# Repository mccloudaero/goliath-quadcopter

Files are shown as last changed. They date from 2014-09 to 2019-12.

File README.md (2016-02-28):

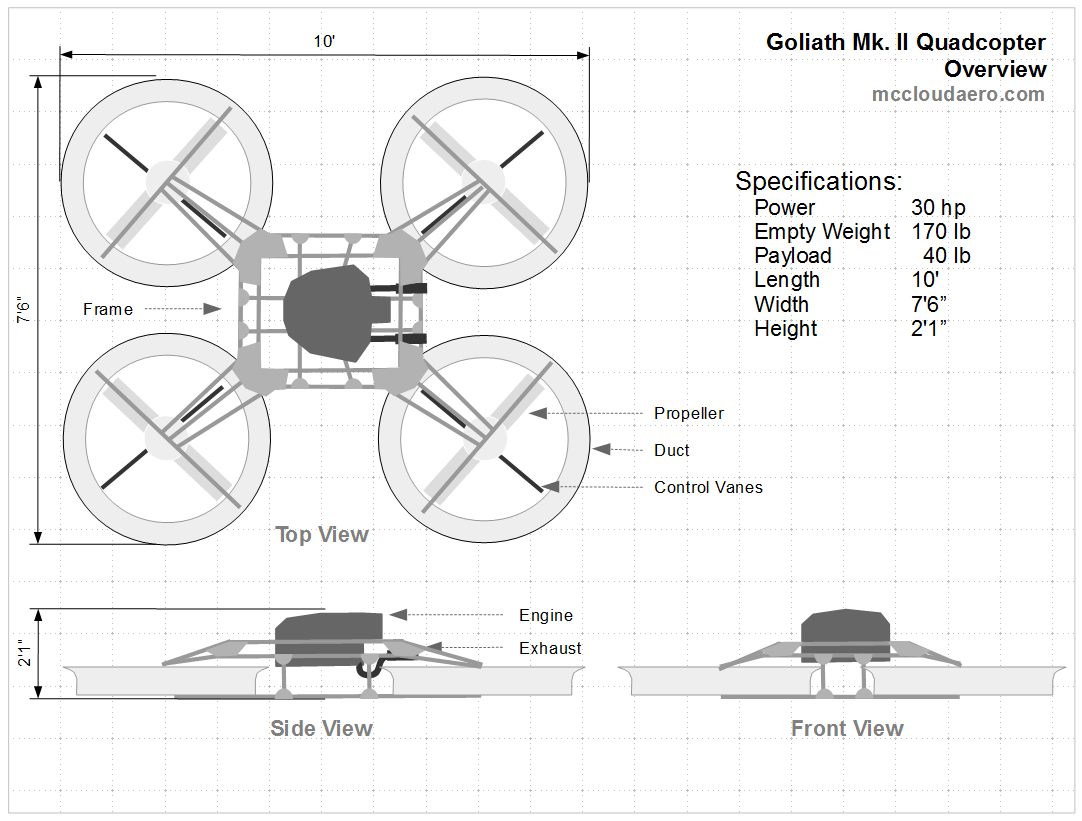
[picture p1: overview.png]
Overview

# Goliath Quadcopter
This repository contains the design data for the Goliath Quadcopter designed by
[McCloud Aero Corp](http://www.mccloudaero.com). The primary documentation source can be found at the
[Hackaday Project Page](https://hackaday.io/project/1230-goliath-a-gas-powered-quadcopter)

### Overview
Goliath is a prototype vehicle for developing large scale quadcopters. The design is based on a single central gas engine with a belt drive providing power to the four propellers. Control is done using control vanes placed under the propellers. Each propeller is enclosed within a duct that protects the rotors and contributes to the lift. Goliath itself will be open source with the creative commons license, and whenever possible open source components were used. It's currently a work in progress, and even when completed it's intended as a starting point for future vehicles.

### [Avionics](https://github.com/mccloudaero/goliath-quadcopter/blob/master/avionics/README.md)
### [Drive System](https://github.com/mccloudaero/goliath-quadcopter/blob/master/drive_system/README.md)
### Electrical System
### Structure

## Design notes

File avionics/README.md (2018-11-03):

# Avionics
### Overview
This file is intended as a guide for setting up the avionics for Goliath. Goliath uses the [Pixhawk2](https://docs.px4.io/en/flight_controller/pixhawk-2.html) flight controller running the [PX4](https://px4.io) flight stack.

## Basic Setup
### Install QGroundControl on your computer
QGroundControl is a software an open source micro air vehicle ground control station [QGroundControl](http://qgroundcontrol.com). In addition to being able to provide mission control for Goliath, it also provides an easy way to load the latest version of the Firmware.

### Controller Setup
The Taranis X9D is the controller recommended for the Pixhawk. General information on setting up the Taranis with the Pixhawk can be found on the Pixhawk user guide at:
[Pixhawk Flight Mode Configuration](http://px4.io/docs/flight-mode-configuration/)
Follow the instructions for setting up the controller for Single Channel Flight Mode Configuration in the video.
[Controller Setup](http://https://youtu.be/scqO7vbH2jo)

####Flight Modes
Switches SE and SF are used together to cycle through the different modes.

Num | Mode | Switch
---|---|---
1|Stabalized/Main|SF back, SE back
2|Acro|SF back, SE mid
3|Altitude Control|SF back, SE front
4|Position Control|SF front, SE front
5|Loiter|SF front, SE mid
6|Return|SF front, SE back

####Goliath specific configuration
Additional channels are required for Goliath to control the gas engine. Setup the controller with the following channels: 

Channel | Source | Function
---|---|---
CH6 | S2 | choke servo
CH7 | SH | starter relay
CH8 | SD | ignition relay

### Firmware Update
Goliath requires special drivers for PX4, and therefore a custom Firmware update. Following the instructions found in /goliath_px4_firmware_patch/README.md

### Customize Configuration
While, the Pixhawk firmware does not require modification, the controller does need custom configuration for Goliath.

Copy /etc in the avionics directory to the SD card.

* /etc/config.txt 
  Sets up the custom configuration for Goliath, specifies which mixers to use 

* /etc/extras.txt 
  Starts the driver for the EVPR master node 

* /etc/mixers
  Custom mixers for goliath

Details on how to make custom mixer files can be found at http://dev.px4.io/concept-mixing.html

#### AUX Servos
The configuration of the Aux output pins is controlled by the fmu app (https://pixhawk.org/firmware/apps/fmu). The mode needed for Goliath's configuration is:
mode_pwm_gpio
This mode enables SRV1-SRV4 and GPIO_EXT1 and GPIO_EXT2

System start-up commands can be changed using the following guide.
http://dev.px4.io/advanced-system-startup.html

More informatition on customization of the PX4 flight stack can be found at:<br>
[Pixhawk: System Startup](http://dev.px4.io/advanced-system-startup.html)<br>
[Pixhawk: Adding A New Airframe](http://dev.px4.io/airframes-adding-a-new-frame.html)

#### Debugging 
Dev Guide on how to connect to the system console:
http://dev.px4.io/advanced-system-console.html

### Theory of Operation
After ensuring that the area is clear, the first step is to set the master switch to ON. At this point the flight controller will power up and start in safe mode (Main LED will be breathing). While in safe mode, all of the servos and relays are disabled from being activated by the firmware. Once it's confirmed that the firmware is operating nominally, the operator can take the system out of safe mode. At this point all of the controls can be checked out prior to starting the engine. If all of the controls are working nominally, the engine can then be started. The engine ignition relay is enabled, allowing the engine to run. Next, the starter is used to start the engine.

### Arming and Disarming
#### From the Control Stick
##### Arming
1. Ensure the Main LED is breathing.
2. Press and hold the safety switch for 3 seconds. The light on the safety switch will start blinking differently.
3. Place the throttle stick in the bottom right corner and hold for 5 seconds. The main LED will become solid.
##### Disarming
To disarm, place the throttle stick in the bottom left corner.

#### Ground Station
Alternatively arming and disarming can also be performed in QGroundControl.

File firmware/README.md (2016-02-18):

# Firmware
### Overview
This file is intended as a guide for setting up the firmware for Goliath. Goliath uses the [Pixhawk](http://www.pixhawk.org) flight controller. The Pixhawk hardware is open source and is capable of running different flight stacks. For Goliath, the PX4 flight stack was chosen.

### Firmware Setup
Before getting started with the firmware, the tool chains need to be setup for compiling the firmware. While the firmware can be compiled on most operating systems, it's really recommended to use Linux, particularly Ubuntu, as it has the most support. The instructions for setting up the tools chains for Linux can be found at:
[Linux Tool Chain Setup](http://dev.px4.io/starting-installing-linux.html)

Once the tool chain has been setup, simply follow the instructions for downloading and compiler the firmware:
[Building the Firmware](http://dev.px4.io/starting-building.html)

### Firmware Configuration
The PX4 flight stack is able to be used for different airframes though the use of mixers. The mixer tells the flight stack how to take the input values and translate them to the output values, so that the control software can be universally applied and eliminates the need for custom firmware. The guide for added custom airframes is at:
[Adding a new Airframe Configuration](http://dev.px4.io/airframes-adding-a-new-frame.html)
[Old Guide - Deprecated](https://pixhawk.org/dev/mixing)

The custom mixer file for Goliath will be located in this folder.

### Theory of Operation
After ensuring that the area is clear, the first step is to set the master switch to ON. At this point the Pixhawk controller will power up and start in safe mode. While in safe mode, all of the servos and relays are disabled from being activated by the firmware. Once it's confirmed that the firmware is operating nominally, the operator can take the system out of safe mode. At this point all of the controls can be checked out prior to starting the engine. If all of the controls are working nominally, the engine can then be started. The engine ignition relay is enabled, allowing the engine to run. Next, the starter is used to start the engine.

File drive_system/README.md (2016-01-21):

# Drive System
### Overview
Goliath uses a single 30 Hp engine and a belt system to transfer power to the four propellers. A single motor was chosen over four smaller engines because of the larger power to weight ratio than a single larger engine. High Torque Drive (HTD) belts were selected because they are able to transfer more power per weight than roller chain and can also run at higher RPMs that Goliath requires.

### Belts vs. Roller Chains
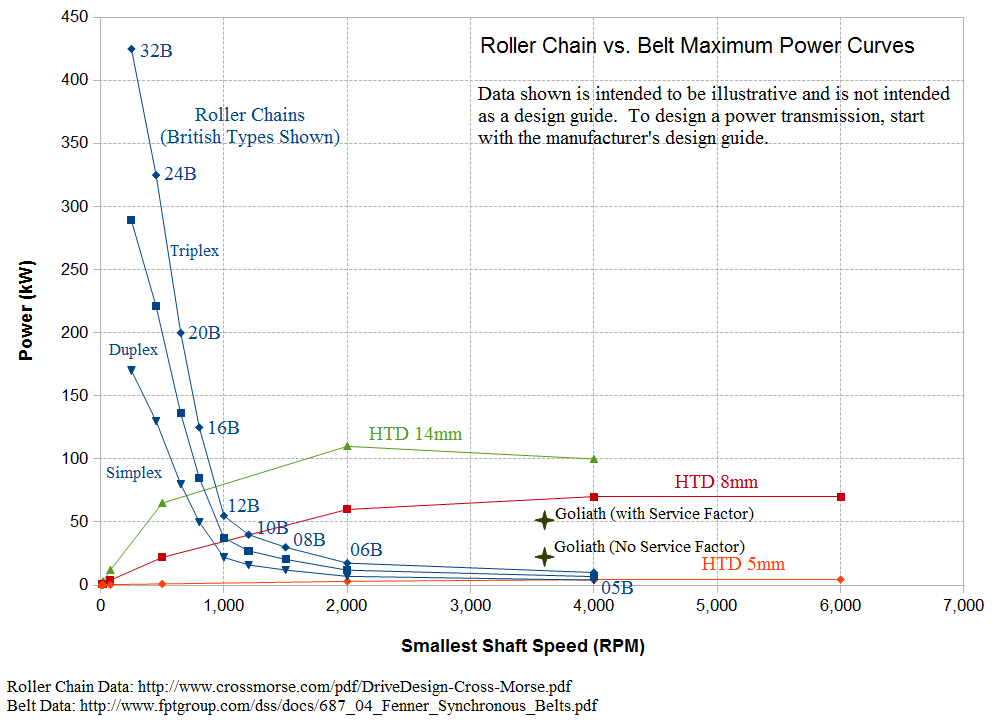
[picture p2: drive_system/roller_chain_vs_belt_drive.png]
Belt vs Rollers


### Belt and Pulley Layout
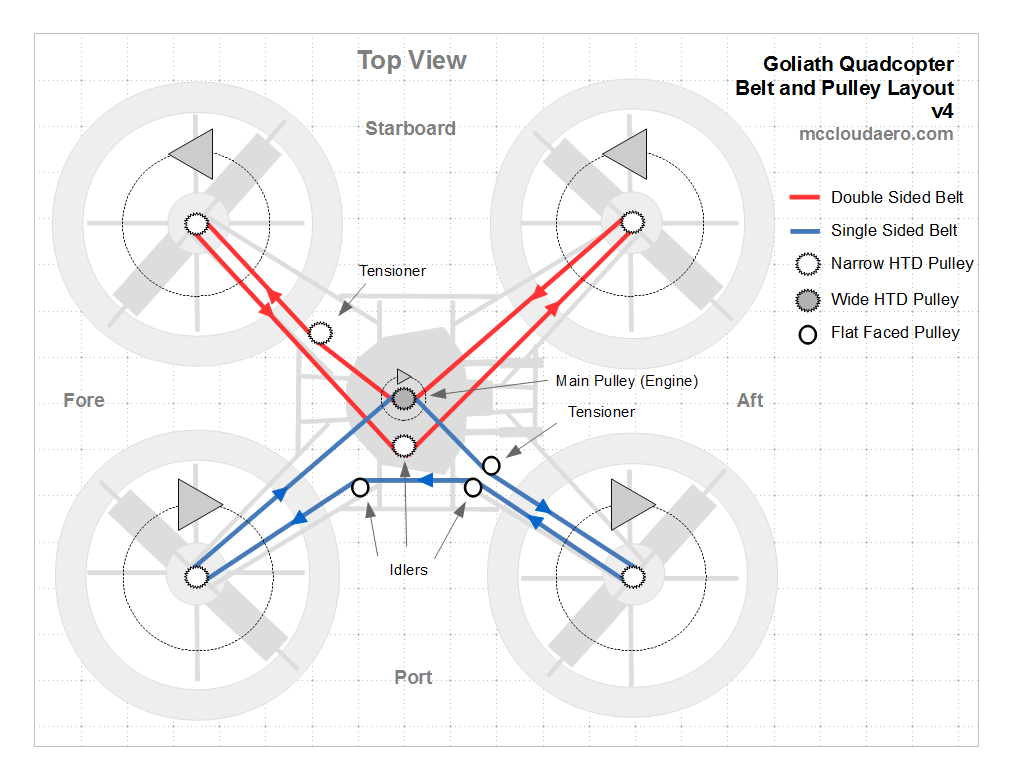
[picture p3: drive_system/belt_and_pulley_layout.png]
Drive System


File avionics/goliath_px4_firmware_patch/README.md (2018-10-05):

# PX4 Firmware patch
Adds drivers for:
* EVPR Master Node
* GPIO Relays

# Firmware Setup
## Checkout Firmware from
https://github.com/PX4/Firmware.git

## Apply Patch
git apply <path to patch>

## Compile
make px4fmu-v3_default

## Flash
make px4fmu-v3_default upload

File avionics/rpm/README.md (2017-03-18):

# RPM Sensor

## Frequency Measurement
The frequency is measured using a hall effect sensor connected to a [Trinket Pro](https://www.adafruit.com/product/2000).

# Trinket Pro
Pin | Purpose
---|---
BAT+|Power to Trinket Pro
GND|Ground
3|Hall Effect Signal
5V(Header)|Hall Effect Power
GND(Header)|Hall Effect Ground 
A4|SDA for I2C
A5|SCL for I2C

## Pixhawk I2C Port pinout
Pin | Signal | Volt
---|---|---
1(red)|VCC|+5
2(blk)|SCL|+3.3(pullups)
3(blk)|SDA|+3.3(pullups)
4(blk)|GND|GND

## References
[Additional Trinket Pro Info] (https://learn.adafruit.com/introducing-pro-trinket/downloads)
[Trinket Pro Pinout] (https://learn.adafruit.com/introducing-pro-trinket/pinouts)

[Adafruit IDE Setup] (https://learn.adafruit.com/adafruit-arduino-ide-setup/overview)

[Hall Effect Sensor Example] (https://diyhacking.com/arduino-hall-effect-sensor-tutorial/)

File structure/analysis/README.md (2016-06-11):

#Analysis Overview
Analysis done with Frame3DD
[Frame3DD](http://frame3dd.sourceforge.net/).

##Linux Install (Ubuntu 14.04)
1. Download Frame3DD source
2. Go to Frame3DD/src and run make
3. mv frame3dd ../
4. ensure gnuplot is installed
5. run

##Run Analysis Case
frame3dd frame.3dd frame.out

##Post-Processing
After the analysis is complete, and the frame design is satisfactory, the results are post-processed. This is done to obtain the total lengths of the tubing required and to get the frame nodes coordinates to build a CAD object.

./framepost.py

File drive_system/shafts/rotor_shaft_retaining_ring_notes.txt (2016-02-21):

Retaining Rings for 3/4" shaft (McMaster-Carr 96363A578)
Groove Width Required: 0.047" (+0.003" -0.000")
Groove Depth Required: 0.023"

Load Capacity 1,218 lbs

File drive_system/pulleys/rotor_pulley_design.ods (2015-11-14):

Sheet: Dimensions
Pulley Type | HTD
Teeth | 40
Tooth Type | 8M
Belt Width | 30 | mm
Pulley Width | 31.877 | mm
Flange Width | 2 | mm
Total Width Required | 35.877 | mm
Idler | SH-BB
Width | 33.3375
Width Difference | 2.5395 | mm | (Positive OK, Negative, need more material)
Bearing
Model | 7868-5tn
Make | Nice
Bore | 5/8”
OD | 40 | mm
Width | 18.25625 | mm | 0.71875 | in
Propeller Thickness | 46.0375 | mm | 1.8125 | in
Bolt Length
Stackup | 81.9145 | mm | 3.224980315 | in
(Pulley+Propeller)
Bolt Length |  |  | 3.75 | in

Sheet: Machining Operations
Machining Operations | Tool
Part Off Pulley | Parting Tool
Center Bore | Drill

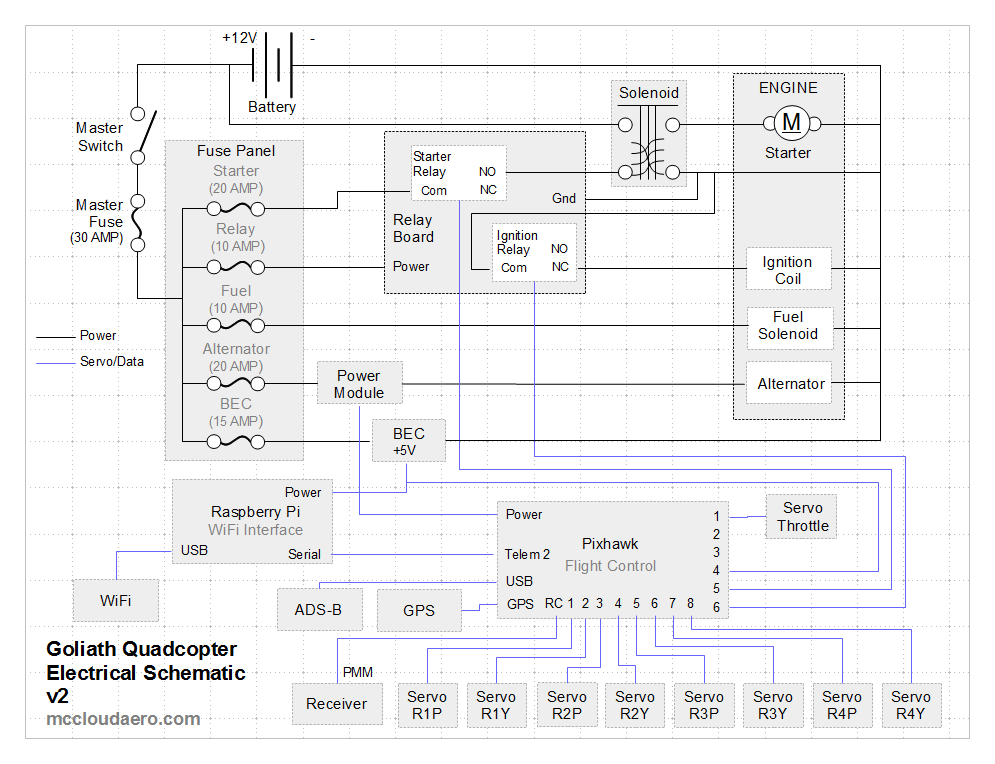
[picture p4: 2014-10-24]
electrical_system/electrical_schematic.png

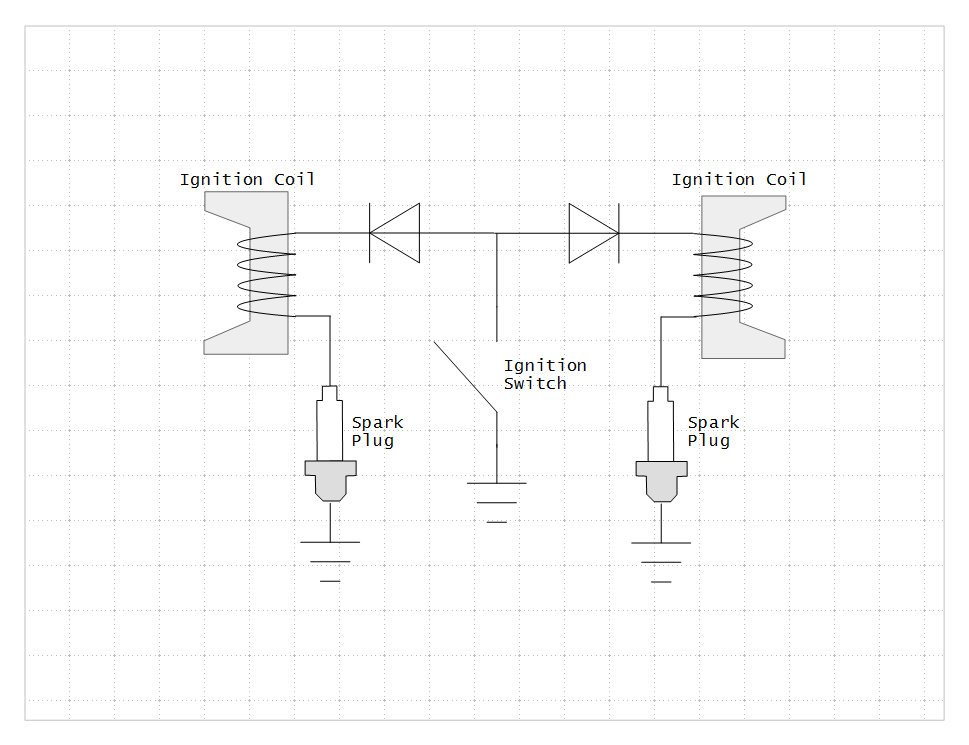
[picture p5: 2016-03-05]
electrical_system/ignition_schematic.png

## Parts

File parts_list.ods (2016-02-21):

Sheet: Parts
Part | Category | Qty | Description | Part No | Supplier | Weight | Sub Total Weight | Price | Sub Total | Link | CAD? | Source | Sub Total | Addtional Info
Engine | Engine | 1 | 1-1/8-Inch by 7/16-20-Inch Shaft Briggs and Stratton Professional Series 30 Gross HP 810 cc V-Twin 1-1/8-Inch by 7/16-20-Inch Shaft | 49M977-1036-G5 | Equipatron | 84.00 | 84.00 | $899.00 | $899.00 | http://www.equipatron.com/briggs-stratton-vertical-engine-49m977-1036-g5.html | No | web | 84 | http://www.briggsandstratton.com/us/en/engines/rider-mower-engines/professional-series-efm
Upper Drive Belt | Drive System | 1 | Double Sided HTD Belt 30mm wide 4960mm Long |  |  | 1.10 | 1.10 |  |  | http://www.bbman.com/catalog/product/4960-8M-20 |  | web | 1.1
Lower Drive Belt | Drive System | 1 | Double Sided HTD Belt 30mm wide 4400mm Long |  |  | 1.10 | 1.10 |  |  | http://www.bbman.com/catalog/product/4400-8M-20 |  | web | 1.1
Engine Bushing | Drive System | 1 | Quick-Disconnect (QD) Bushing Style SH, 1-1/8" Bore, 1/4" x 1/8" Keyway | SHX1-1/8 | B&B Manufacturing | 1.00 | 1.00 | $9.50 | $9.50 | http://www.bbman.com/catalog/product/SHX1-1_8 | Yes | web | 1
Engine Pulley | Drive System | 1 | Pulley 8mm Pitch, 50mm Wide Belt, QD Bushing, Style SH, 3.819" OD, 34 Teeth | QD34-8M-50 | B&B Manufacturing | 2.60 | 2.60 | $84.00 | $84.00 | http://www.bbman.com/catalog/product/QD34-8M-50 | Yes | web | 5.2
Rotor Pulley | Drive System | 4 | Pulley 8mm Pitch, 30mm Wide 44 Teeth |  | McCloud Aero | 1.75 | 7.00 | $101.59 | $406.36 |  | Yes | web | 5.52
Rotor (CW) |  | 2 |  |  | McCloud Aero | 1.25 | 2.50 | $30.00 | $60.00 |  | Yes | est | 20
Rotor (CCW) |  | 2 |  |  | McCloud Aero | 1.25 | 2.50 | $30.00 | $60.00 |  | Yes | est | 20
Rotor Bolt | Drive System | 24 | 1/4”-20 bolts 3 3/4” long, grade 8 | 91257A557 | McMaster-Carr |  | 0.00 | $0.51 | $12.87
Rotor Shaft | Drive System | 4 | 5/8” diameter, 12” long shaft | 5947k14 | McMaster-Carr | 1.25 | 5.00 | 12.13 | $48.52 | http://www.mcmaster.com/#5947k14/=zzzib2
Center Beam – A | Structure | 1 | Slotted Angle 2 1/2” x 1 1/2” x 39 3/4” |  |  | 2.78 | 2.78
Center Beam – B | Structure | 1 | Slotted Angle 2 1/2” x 1 1/2” x 39 3/4” |  |  | 2.78 | 2.78
Center Beam – C | Structure | 1 | Slotted Angle 1 1/2” x 1 1/2” x 39 3/4” |  |  |  | 0.00
Center Beam – D | Structure | 1 | Slotted Angle 1 1/2” x 1 1/2” x 39 3/4” |  |  |  | 0.00
End Beam | Structure | 4 | Slotted Angle 2 1/2” x 1 1/2” x 18” |  |  | 1.26 | 5.04
Cross Beam | Structure | 4 | Slotted Angle 2 1/2” x 1 1/2” x 30” |  |  | 2.10 | 8.40
Side Beam – A | Structure | 2 | Slotted Angle 2 1/2” x 1 1/2” x 29 1/4” |  |  | 2.05 | 4.10
Side Beam – B | Structure | 2 | Slotted Angle 2 1/2” x 1 1/2” x 29 1/4” |  |  | 2.05 | 4.10
Prop Mount | Structure | 8 | Slotted Angle 2 1/2” x 1 1/2” x 6” |  |  | 0.42 | 3.36
Outer Prop Support | Structure | 8
Inner Prop Support – A | Structure | 4
Inner Prop Support – B | Structure | 4
Side Cross Bar | Structure | 4 | Slotted Flat 1 1/2” x 30” |  |  |  | 0.00
End Cross Bar | Structure | 4 | Slotted Flat 1 1/2” x 18” |  |  |  | 0.00
Engine Bolts | Structure | 4
 |  |  |  |  |  |  | 137.355

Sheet: Raw Materials
Material | Qty | Part No. | Supplier | Price | Sub-Total | Weight (lbf) /Inch
Slotted Angle 2-1/2”x1-1/2”x72” | 7 | 470-658 | Home Depot | $21.51 | $150.57 | 0.0691823899
Slotted Angle 1-1/2”x1-1/2”x72” | 9 | 254-665 | Home Depot | $16.48 | $148.32
Slotted Flat 1-3/8” x 1/16” x 72” | 3 | 584-328 | Home Depot | $9.76 | $29.28
Slotted Flat 2-13/16” 14ga x 60” | 1 | 5215827 | Ace Hardware | $9.00 | $9.00
All Thread 5/8-11 x 36” | 2 | 671-266 | Home Depot | $6.57 | $13.14
All Thread 1/2-13 x 36” | 1 | 671-258 | Home Depot | $4.71 | $4.71
All Thread 3/8-16 x 36” | 2 | 671-223 | Home Depot | $2.87 | $5.74
All Thread 5/16-18 x 36” | 5 | 671-215 | Home Depot | $2.63 | $13.15
Square Tube – 1” x 1/16” x 48” | 1 | 368-202 | Home Depot | $14.42 | $14.42
Sheet Metal Zinc 26ga 12”x24” | 2 | 476-04? | Home Depot | $6.97 | $13.94
 |  |  |  | Materials Total | $402.27

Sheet: Rotor Pulley
Part | Qty | Description | Part No | Supplier | Price | Sub Total | Link
Pulley Stock | 1/5 | Raw Pulley Stock | 3H-040-8MM-HTD-10-A | H&M | $168.75 | $33.75 | http://www.hmmanufacturing.com/store/p1354/3H-040-8MM-HTD-10-A.html
Pulley Flange | 1/8 | Flange |  | H&M | $103.84 | $12.98 | http://www.hmmanufacturing.com/store/p1354/3H-040-8MM-HTD-10-A.html
Bearing | 2 | Nice Bearing 5/8” ID | 2780T43 | McMaster-Carr | $18.41 | $36.82 | http://www.mcmaster.com/#2780t43/=11584m4
 |  |  |  |  | Raw Pulley | $46.73
 |  |  |  |  | With Bearings | $83.55

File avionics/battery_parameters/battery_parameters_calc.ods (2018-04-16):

Battery Setting Calculations
Number of Cells | Total Voltage Max | Total Voltage Min | Total Voltage Drop Under Load | Cell Voltage Max | Cell Voltage Min | Cell Voltage Drop Under Load
6 | 13.2 | 10.5 | 4 | 2.2 | 1.75 | 0.6666666667

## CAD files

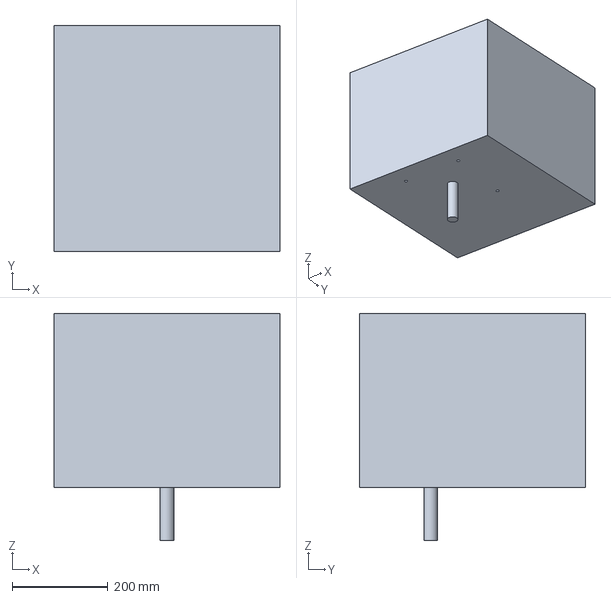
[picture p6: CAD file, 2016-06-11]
drive_system/engine/engine.stp
472.7 x 473.2 x 474.9 mm

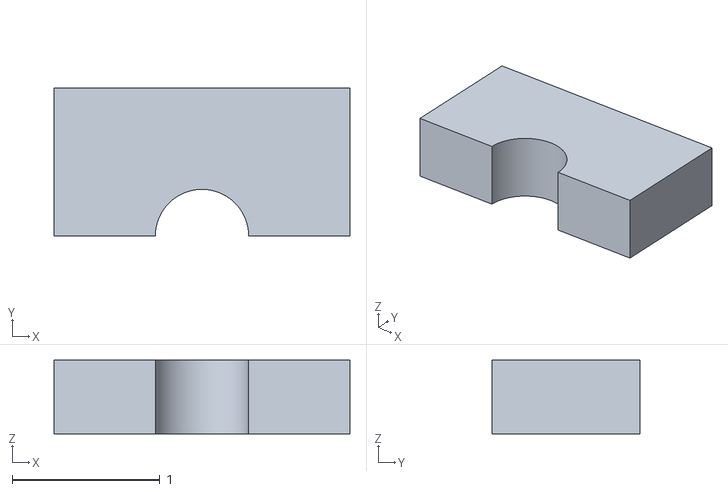
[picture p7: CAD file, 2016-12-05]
structure/idler_shaft_mount/idler_shaft_mount_no_holes.stl
2.00 x 1.00 x 0.5

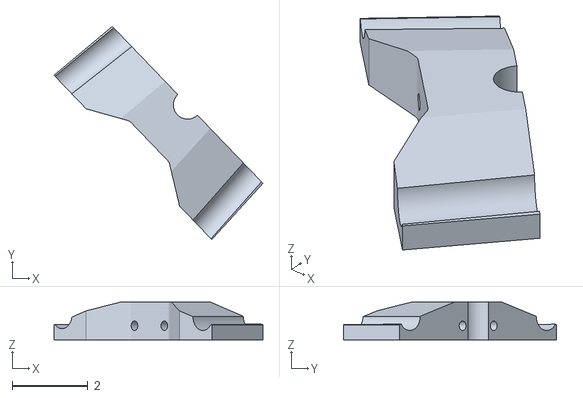
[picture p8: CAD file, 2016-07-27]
structure/rotor_shaft_mount/rotor_shaft_mount_C.stl
5.50 x 5.62 x 1.00

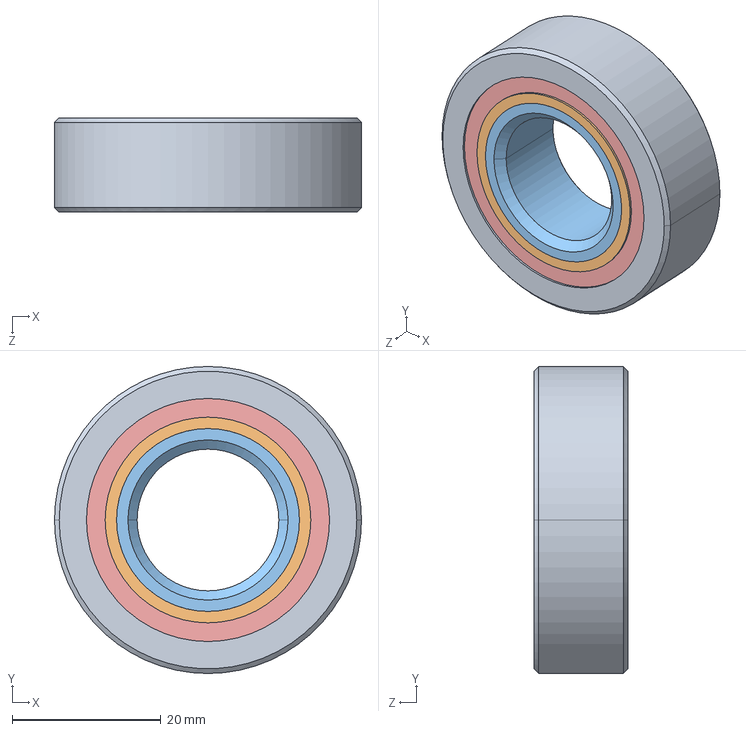
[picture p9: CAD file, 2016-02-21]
drive_system/pulleys/2780T43.STEP
41.3 x 41.3 x 12.7 mm

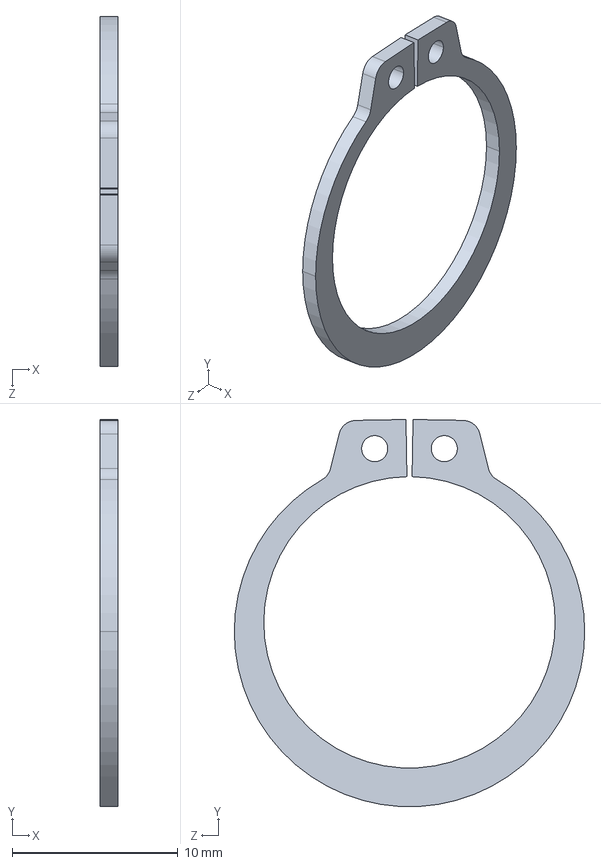
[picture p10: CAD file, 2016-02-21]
drive_system/shafts/96363A578.STEP
1.07 x 23.4 x 21.2 mm

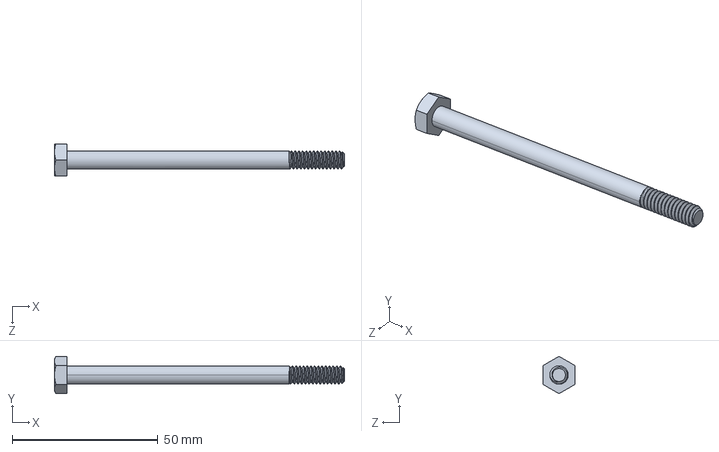
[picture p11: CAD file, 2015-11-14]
drive_system/pulleys/91257A557.STEP
99.6 x 12.8 x 11.1 mm

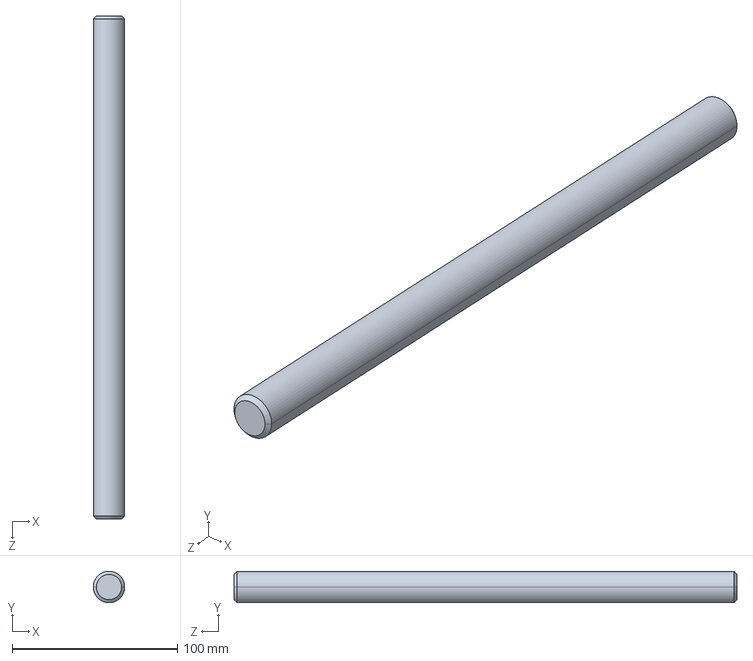
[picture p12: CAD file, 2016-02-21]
drive_system/shafts/5947K150.STEP
19.0 x 19.0 x 304.8 mm

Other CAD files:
structure/rotor_shaft_mount/rotor_shaft_mount_A.stl

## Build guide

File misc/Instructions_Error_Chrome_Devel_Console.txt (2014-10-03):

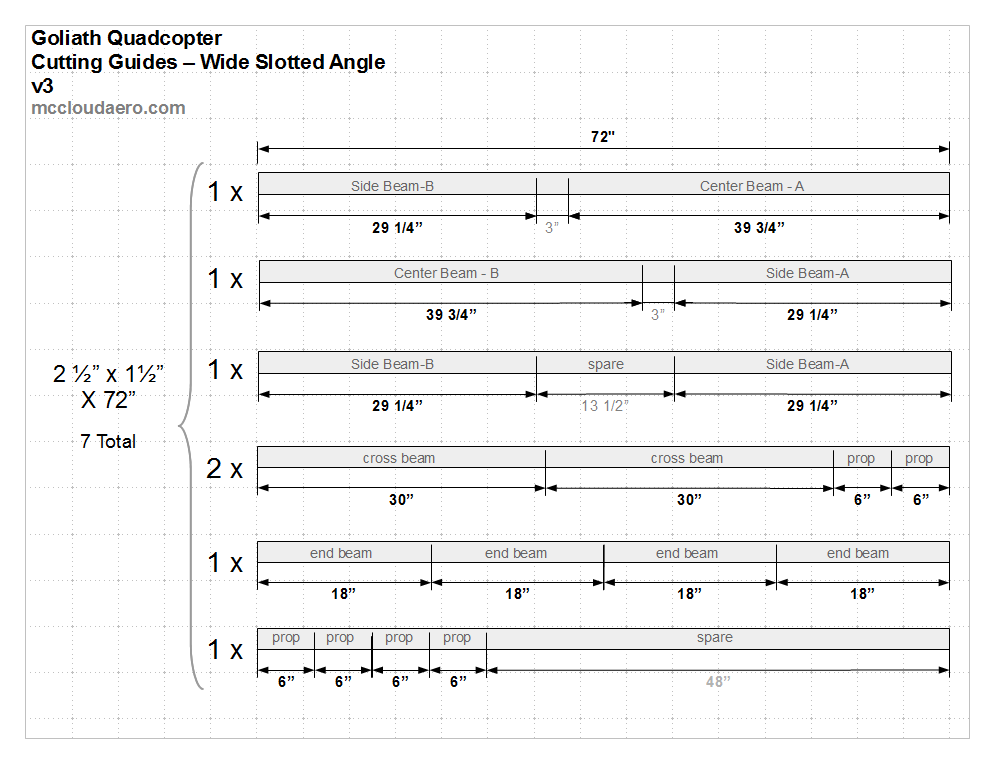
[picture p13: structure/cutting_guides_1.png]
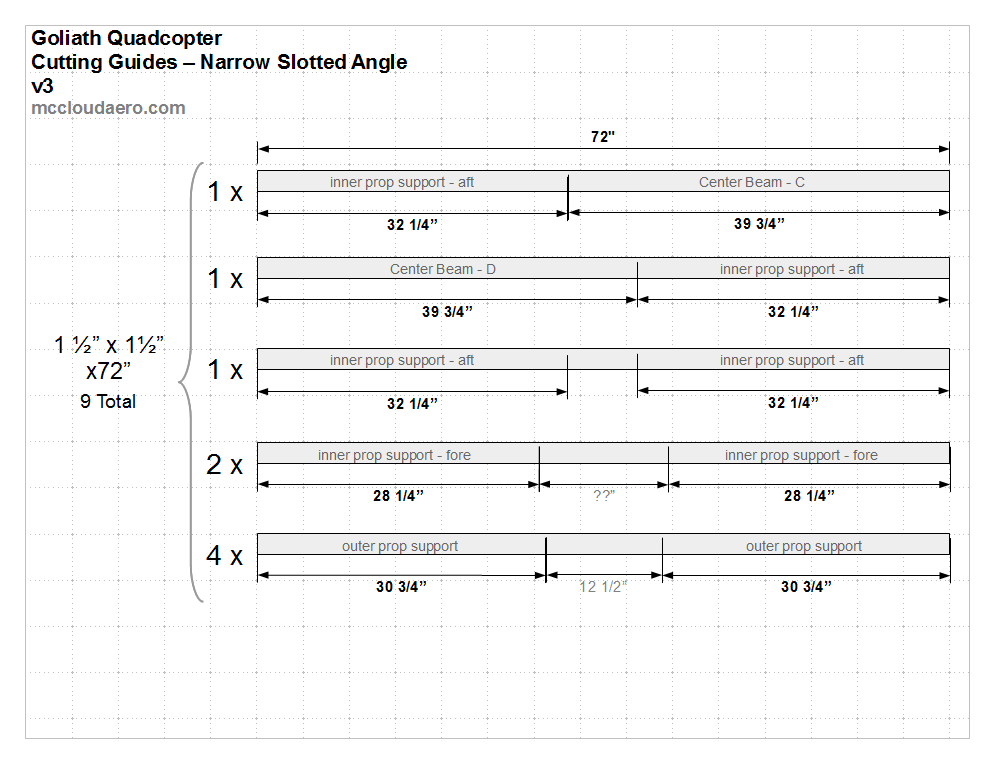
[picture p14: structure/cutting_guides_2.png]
Uncaught SyntaxError: Invalid regular expression: /</p><p>Afterwards be sure to file all the edges and corners.</p><p>The pieces after being cut are:</p><ul><li>4×&nbsp;Center Beams ( 2 1/2" x 1 1/2" x 39 3/4")</li><li>4×&nbsp;Side Beams ( 2 1/2" x 1 1/2" x 29 1/4" )</li><li>4×&nbsp;Cross Beams ( 2 1/2" x 1 1/2" x 30" )</li><li>4×&nbsp;End Beams ( 2 1/2" x 1 1/2" x 18" )</li><li>8×&nbsp;Outer Prop Supports ( 1 1/2" x 1 1/2" x 30 3/4" )</li><li>4×&nbsp;Inner Prop Supports - Fore ( 1 1/2" x 1 1/2" x 28 1/4" )</li><li>4×&nbsp;Inner Prop Supports - Aft ( 1 1/2" x 1 1/2" x 32 1/4" )</li><li>8×&nbsp;Shaft Mounts - ( 2 1/2" x 1 1/2" x 6")</li><li>4×&nbsp;End Cross Bars ( 1 1/2" x 1/16" x 18" )</li><li>4×&nbsp;Side Cross Bars ( 1 1/2" x 1/16" x 30"&nbsp;)</li><li>1×&nbsp;Battery Plate ( 2 3/4" x 1/16" x 11 1/4" )</li></ul><h2>B) Assemble the Top and Bottom Decks</h2><p>Follow steps B1 and B2 for each deck</p><p><em>Note: The frame assembly uses only 5/16" bolts. &nbsp;All of the bolts, lock washers and hex nuts referenced will all be 5/16"</em></p><p style="margin-left: 20px;"><span style="font-size: 16px; background-color: initial;" data-verified="redactor">/: Unmatched ')'

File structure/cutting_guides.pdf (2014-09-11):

4 x

39 3/4” | 29 1/4” | 3”
2 x
30” | 30” | 6” | 6”

1 x

18” | 18” | 18” | 18”

1 x

## Goliath Quadcopter Cutting Guides – Slotted Angle

v1

### mccloudaero.com

center beam | side beam
cross beam | cross beam
end beam | end beam | end beam | end beam
prop | prop

4 x

30 3/4” | 30 3/4” | 12 1/2”
outer prop support | outer prop support

4 x

28 1/4” | 32 1/4” | 13 1/2”
inner prop support - fore | inner prop support - aft

## 2 ½” x 1½”

X 72”

## 1 ½” x 1½”

x72”

72"

## 8 Total

## 8 Total

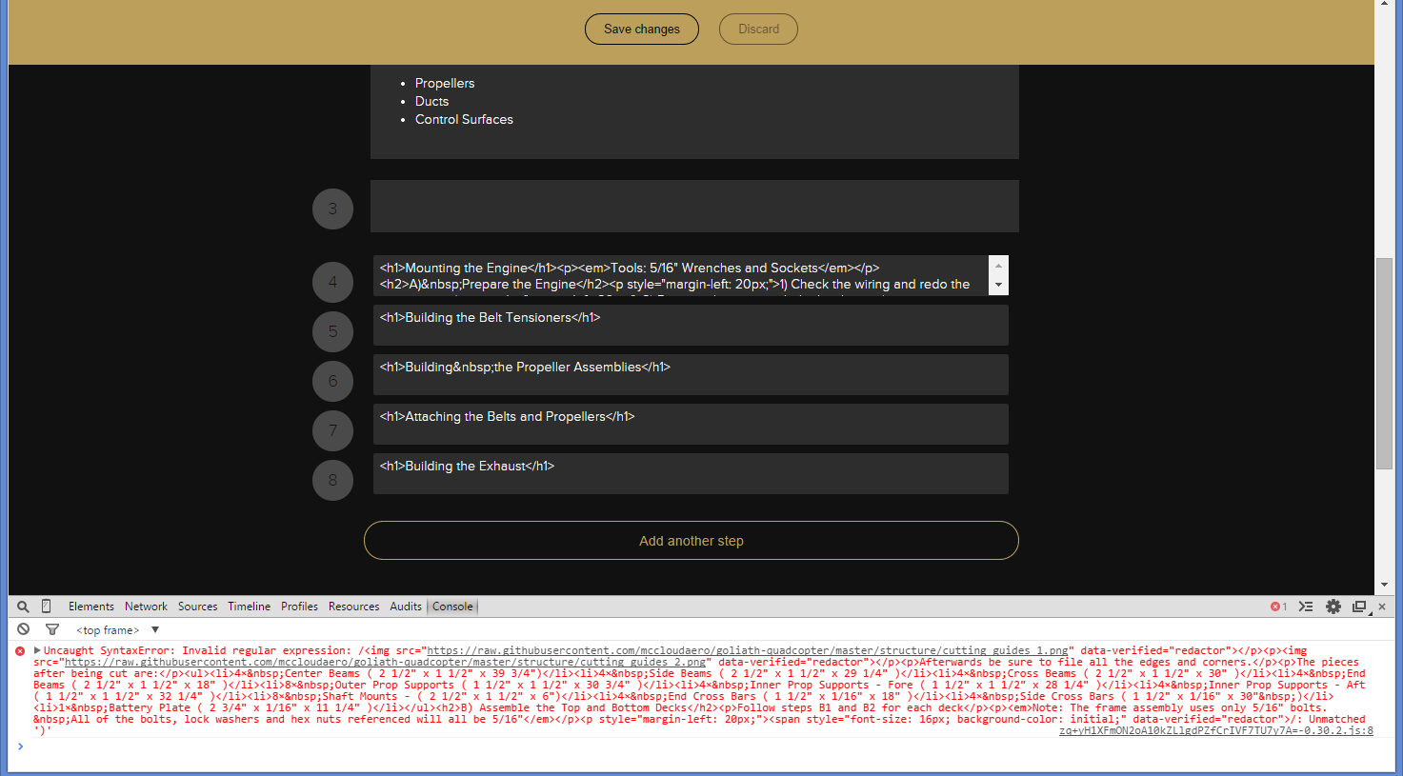
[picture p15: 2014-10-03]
misc/Instructions_Errors_Chrome_Devel_Console.png

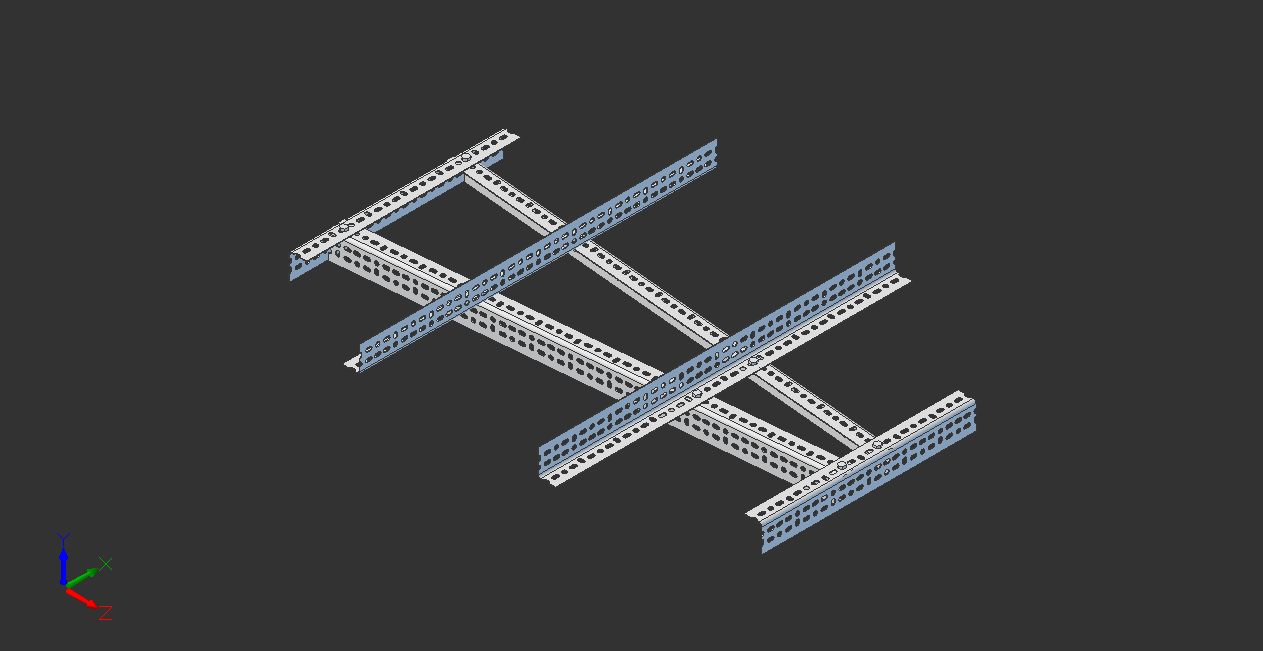
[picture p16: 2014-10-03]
structure/instructions/deck_step2_complete.png

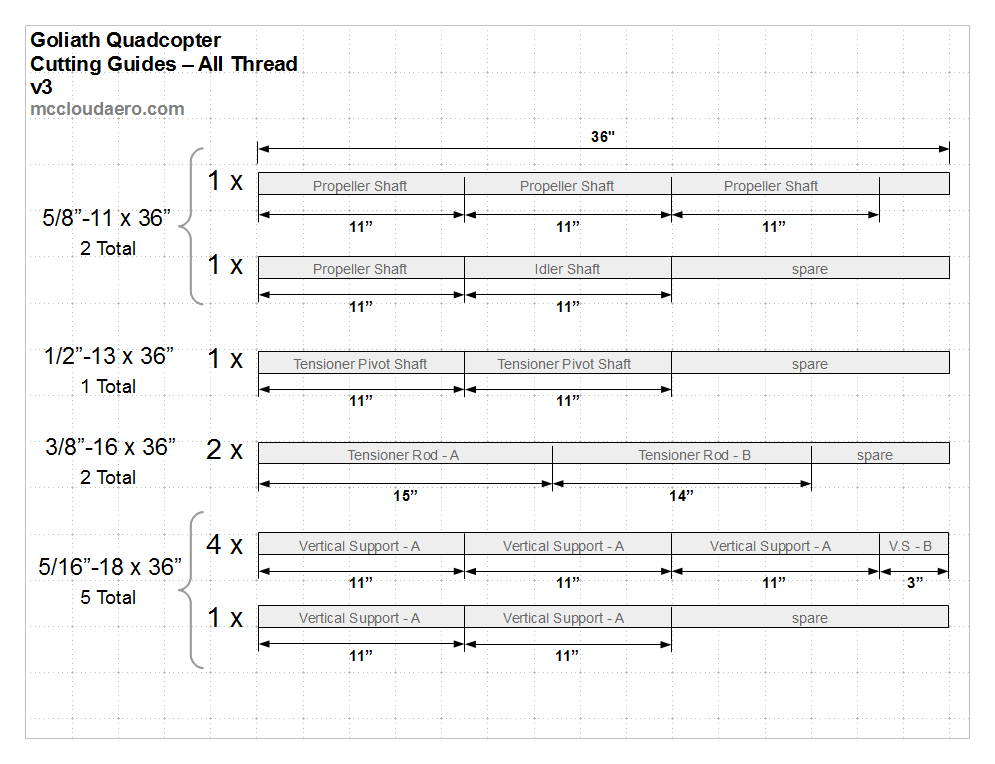
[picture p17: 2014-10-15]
structure/cutting_guides_4.png

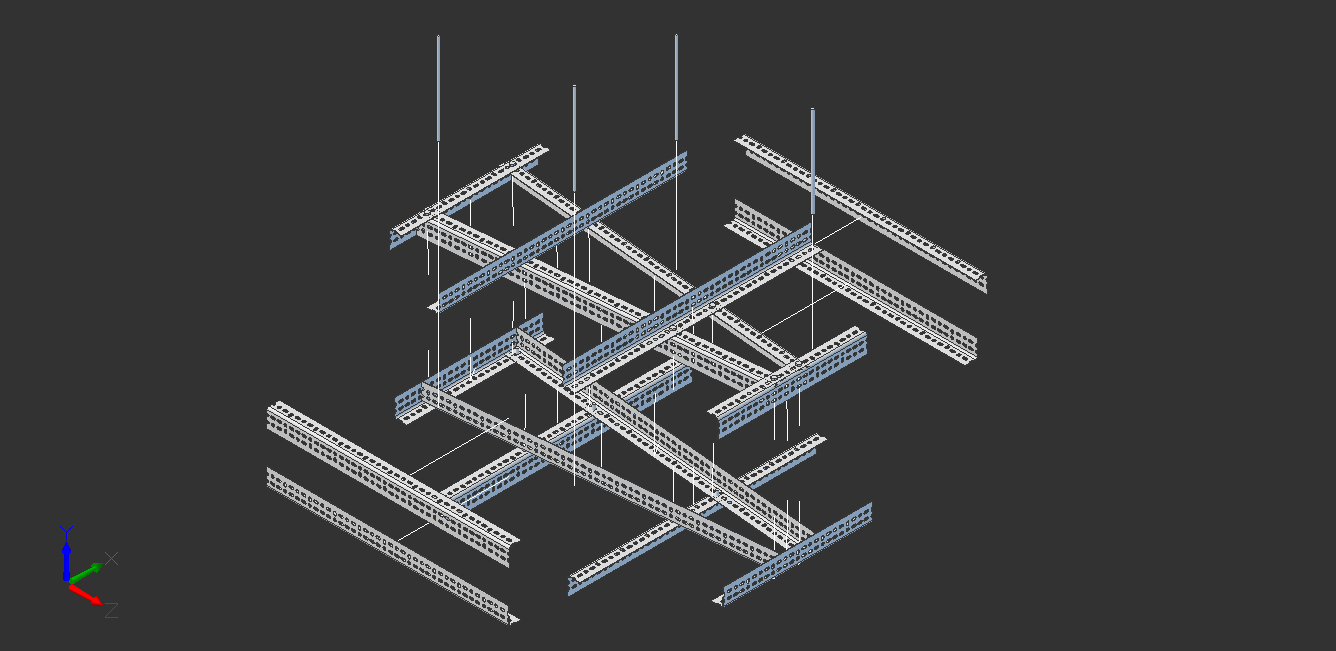
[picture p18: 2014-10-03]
structure/instructions/join_decks_exploded.png

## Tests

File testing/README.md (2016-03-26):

# Testing 
This folder contains test data recorded from the flight controller (Pixhawk)
[Test_48](http://logs.uaventure.com/view/cbyxxUfE2HFdGtMKeWBhwD): First test with Pixhawk on-board 
[Test_49](http://logs.uaventure.com/view/3cFswJqd69yKLvAQTJ8tHX): Second test with Pixhawk on-board, new isolation setup

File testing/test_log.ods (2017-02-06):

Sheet: Mk. II
 |  | 00:48:55
Test | Date | Test Duration | Running Time | Purpose | Results | Details | YouTube Video
1 | 2016-09-06 | 00:01:53 | 00:01:53 | First Mk. II run, check out hardware | Success, Main pulley came loose | Project Log (https://hackaday.io/project/1230/log/45279-goliath-mk-ii-hovers) | https://www.youtube.com/watch?v=ZzuZMFTv0l8
2 | 2016-09-07 | 00:01:24 | 00:03:17 | Hover Attempt | Partial hover, center of gravity off | Project Log (https://hackaday.io/project/1230/log/45279-goliath-mk-ii-hovers) | https://www.youtube.com/watch?v=ZzuZMFTv0l8
3 | 2016-09-07 | 00:02:10 | 00:05:27 | Hover Attempt | Success, Hover | Project Log (https://hackaday.io/project/1230/log/45279-goliath-mk-ii-hovers) | https://www.youtube.com/watch?v=ZzuZMFTv0l8
4A | 2016-09-30 | 00:01:40 | 00:07:07 | Checkout, Warmup | Success
4B | 2016-09-30 | 00:01:19 | 00:08:26 | Hover Attempt | Partial hover, starboard doesn't lift
4C | 2016-09-30 | 00:01:19 | 00:09:45 | Hover Attempt with 10 lb Weight to offset cg | Partial hover, front doesn't lift
4D | 2016-09-30 | 00:00:58 | 00:10:43 | Hover Attempt with 10 lb Weight to offset cg | Partial hover, bucks front to back
4E | 2016-09-30 | 00:01:26 | 00:12:09 | Hover Attempt | Partial hover with looser lines, moves wildly back and forth. Later found that the port exhaust came loose.
5A | 2016-10-02 | 00:02:21 | 00:14:30 | Testing New Al Tensioner Pulley | Success, found the port exhaust was loose.
5B | 2016-10-06 | 00:03:27 | 00:17:57 | Testing New Al Tensioner Pulley, Hover Attempt | Success, Hovered for 25s, port exhaust came loose.
6 | 2016-11-04 | 00:04:42 | 00:22:39 | Testing Final Al Pulleys | Success, port exhaust bolts come completely undone. Temp avionics tray comes loose.
7 | 2016-11-06 | 00:00:59 | 00:23:38 | Testing Exhaust Repairs | Success
8 | 2016-11-11 | 00:03:57 | 00:27:35 | Testing New Avionics Tray, Hover Attempt | Success, Partial hover, starboard doesn't lift
9 | 2016-11-13 | 00:03:35 | 00:31:10 | Testing Pixhawk | Pixhawk lost Power On start-up. Battery having issues.
10A | 2016-11-17 |  | 00:31:10 | Testing Pixhawk | Solenoid Fails
10B | 2016-11-18 | 00:02:16 | 00:33:26 | Testing Pixhawk | Success, Recorded Pixhawk data
11 | 2016-11-19 | 00:02:28 | 00:35:54 | Testing Pixhawk, Hover Attempt | Recorded Pixhawk data, Partial hover, starboard side won't lift
12 | 2016-11-20 | 00:01:57 | 00:37:51 | Testing Rotor Aerodynamics with Tufts | Success, Partial hover, starboard side won't lift
13 | 2016-12-27 | 00:04:45 | 00:42:36 | Testing New Idler Shafts and Exhaust | Success
14 | 2017-01-27 | 00:03:05 | 00:45:41 | Testing Tensioner Shaft and Pixhawk Pass-through | Success
15 | 2017-02-01 | 00:03:14 | 00:48:55 | Testing Outside Test Stand | Success

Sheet: Mk. I
 |  | 00:09:03
Test | Date | Test Duration | Running Time | Purpose | Results | Details | YouTube Video
1 | 2014-08-29 | 00:00:06 | 00:00:06 | Run on Starter Only to Check out Hardware | Success | Project Log (https://hackaday.io/project/1230-goliath-a-gas-powered-quadcopter/log/9314-hover-testingbroken-vehicle) | https://www.youtube.com/watch?v=XSjYH7lru0w
2 | 2014-09-01 | 00:00:06 | 00:00:12 | Run on Gas for the first time | Loss of Tension, Broken Parts | Project Log (https://hackaday.io/project/1230-goliath-a-gas-powered-quadcopter/log/9314-hover-testingbroken-vehicle) | https://www.youtube.com/watch?v=mCfh3zFHTus
3 | 2014-10-06 | 00:00:05 | 00:00:17 | Run on Starter Only to Check New Tensioner | Success | Project Log (https://hackaday.io/project/1230/log/10299-testing-round-2) | https://www.youtube.com/watch?v=ZJ6dnGEMr3Q
4 | 2014-10-08 | 00:00:08 | 00:00:25 | Run on Starter Only to Check Belt Guards | Success | Project Log (https://hackaday.io/project/1230/log/10299-testing-round-2) | https://www.youtube.com/watch?v=k4okZdfEIZs
5 | 2014-10-11 | 00:00:23 | 00:00:48 | Run on Gas for the first time, single sided belt | Success | Project Log (https://hackaday.io/project/1230/log/10299-testing-round-2) | https://www.youtube.com/watch?v=Xh04DMtYJIM
6 | 2014-10-13 | 00:00:38 | 00:01:26 | Run on Gas with both belts | Success | Project Log (https://hackaday.io/project/1230/log/10299-testing-round-2) | https://www.youtube.com/watch?v=CThhOUNxjRo
7 | 2014-10-13 | 00:01:02 | 00:02:28 | Run on Gas with both belts | Success | Project Log (https://hackaday.io/project/1230/log/10522-conclusions-from-round-2-of-testing-and-next-steps) | https://www.youtube.com/watch?v=5GBx1uHGSno
8 | 2014-10-16 | 00:01:31 | 00:03:59 | Run on Gas with both belts | Success | Project Log (https://hackaday.io/project/1230/log/10522-conclusions-from-round-2-of-testing-and-next-steps) | https://www.youtube.com/watch?v=s_NvtabTg0I
9 | 2014-11-15 | 00:00:19 | 00:04:18 | Checking out Test Stand | Success | Project Log (https://hackaday.io/project/1230/log/11118-tests-9-and-10-checking-out-the-test-stand) | https://www.youtube.com/watch?v=KvBA0cagbM8
10 | 2014-11-15 | 00:00:14 | 00:04:32 | Checking out Test Stand | Success | Project Log (https://hackaday.io/project/1230/log/11118-tests-9-and-10-checking-out-the-test-stand) | https://www.youtube.com/watch?v=KvBA0cagbM8
11 | 2014-11-18 | 00:00:22 | 00:04:54 | Testing Belt Configurations | Success | Project Log (https://hackaday.io/project/1230-goliath-a-gas-powered-quadcopter/log/11340-testing-belt-configurations-tests-11-14) | https://www.youtube.com/watch?v=gJ8lPIxMRAI
12 | 2014-11-18 | 00:00:16 | 00:05:10 | Testing Belt Configurations | Success | Project Log (https://hackaday.io/project/1230-goliath-a-gas-powered-quadcopter/log/11340-testing-belt-configurations-tests-11-14) | https://www.youtube.com/watch?v=gJ8lPIxMRAI
13 | 2014-11-22 | 00:00:19 | 00:05:29 | Testing Belt Configurations | Success | Project Log (https://hackaday.io/project/1230-goliath-a-gas-powered-quadcopter/log/11340-testing-belt-configurations-tests-11-14) | https://www.youtube.com/watch?v=gJ8lPIxMRAI
14 | 2014-11-22 | 00:00:21 | 00:05:50 | Testing Belt Configurations | Success | Project Log (https://hackaday.io/project/1230-goliath-a-gas-powered-quadcopter/log/11340-testing-belt-configurations-tests-11-14) | https://www.youtube.com/watch?v=gJ8lPIxMRAI
15 | 2015-01-16 | 00:00:10 | 00:06:00 | Testing Wider Belt | Throttle Linkage Disconnects | Project Log (https://hackaday.io/project/1230-goliath-a-gas-powered-quadcopter/log/12940-test-15-and-16-complete) | https://www.youtube.com/watch?v=_qdGT2g1irE
16 | 2015-01-16 | 00:00:16 | 00:06:16 | Testing Wider Belt | Success | Project Log (https://hackaday.io/project/1230-goliath-a-gas-powered-quadcopter/log/12940-test-15-and-16-complete) | https://www.youtube.com/watch?v=_qdGT2g1irE
17 | 2015-02-14 | 00:00:23 | 00:06:39 | Testing Both Wider Belts | Success | Project Log (https://hackaday.io/project/1230-goliath-a-gas-powered-quadcopter/log/14145-double-sided-belt-added-first-full-throttle-test) | https://www.youtube.com/watch?v=7cZ_y-8LQAs
18 | 2015-02-15 | 00:00:25 | 00:07:04 | Testing Both Wider Belts, Bigger Tensioner | Success | Project Log (https://hackaday.io/project/1230-goliath-a-gas-powered-quadcopter/log/14145-double-sided-belt-added-first-full-throttle-test) | https://www.youtube.com/watch?v=7cZ_y-8LQAs
19 | 2015-02-15 | 00:00:50 | 00:07:54 | Testing Both Wider Belts, Bigger Tensioner, Extra Pulley Full Throttle | Success | Project Log (https://hackaday.io/project/1230-goliath-a-gas-powered-quadcopter/log/14145-double-sided-belt-added-first-full-throttle-test) | https://www.youtube.com/watch?v=7cZ_y-8LQAs
20 | 2015-03-18 | 00:01:09 | 00:09:03 | Testing Load Cells | Prop Bolt Breaks | Project Log (https://hackaday.io/project/1230-goliath-a-gas-powered-quadcopter/log/15456-progress-on-the-test-stand-and-broken-bolts) | https://www.youtube.com/watch?v=VdbsInndI-k

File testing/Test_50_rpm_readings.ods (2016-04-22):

Test 50
Throttle (%) | RPM
Starter | 510
0 | 1740
25 | 2190
50 | 2850
75 | 3210
100 | 3240

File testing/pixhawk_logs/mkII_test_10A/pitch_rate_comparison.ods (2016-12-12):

MK I Test 48 | MK II Test 10A
ATT_PitchRate | ATT_PitchRate
0.0020914394 | -0.0071902713
0.0010320181 | -0.0068698749
0.0017686458 | -0.0070789438
0.0020984774 | -0.0074162474
0.0013454705 | -0.0071561169
0.0015522474 | -0.006877007
0.0019925945 | -0.0069142086
0.0019925945 | -0.0064888187
0.0016574403 | -0.0066451263
0.0010129586 | -0.0071815262
0.0017439611 | -0.0073337415
0.0017284853 | -0.0076693539
0.0009695031 | -0.0076871244
0.0009582508 | -0.0070220679
0.000959482 | -0.0064297235
0.0019038934 | -0.0060794083
0.0011514844 | -0.0058632763
0.0014568642 | -0.0059837727
0.000705068 | -0.0062430641
0.0019828016 | -0.006417484
0.001134471 | -0.0061791586
0.0009143725 | -0.0062556621
0.0007080454 | -0.0060464963
0.0011312859 | -0.0061812401
0.0007099593 | -0.0063078534
0.0021996778 | -0.0063468674
0.0008241888 | -0.0061737681
0.0020006374 | -0.0063321581
0.0009362632 | -0.0066819936
0.0014798474 | -0.0068689184
0.0018000901 | -0.0069044633
0.0014872905 | -0.0067019621
0.0017044693 | -0.00657521
0.0023580557 | -0.0060958574
0.0007689148 | -0.0059153773
0.0015044119 | -0.0064935703
0.0009880327 | -0.0067765573
0.000459196 | -0.0068430584
0.0015212595 | -0.006996558
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

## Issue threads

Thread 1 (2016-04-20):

Engine Data

petermccloud, 2016-04-20:
Need Engine mount information for new frame design. Add:

1. Datasheet
2. CAD Object

petermccloud, 2016-04-28:
Engine data was added under al_frame branch at:
https://github.com/mccloudaero/goliath-quadcopter/tree/al_frame/drive_system/engine

Closed 2016-04-28.

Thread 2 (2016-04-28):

structure loads need to be compiled

petermccloud, 2016-04-28:
Loads need to be defined for the structure. Major items are:
1. Rotor Loads
2. Belt Loads

petermccloud, 2018-11-02:
Not needed anymore

Closed 2018-11-02.

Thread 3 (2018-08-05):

Vehicle Hard Mounts

petermccloud, 2018-08-05:
Add hard mounts to replace ropes. Rope ends occasionally clip rotors

petermccloud, 2018-11-02:
Completed hard mounts. Design info added in [commit](https://github.com/mccloudaero/goliath-quadcopter/commit/cee04f8af74f996b7a5e6ce0dfba5f09dc4a8e1e)

Closed 2018-11-02.

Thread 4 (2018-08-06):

PX4 mixer issue

petermccloud, 2018-08-06:
Current custom mixer does not work with PX4 v1.7.3.

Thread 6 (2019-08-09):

Re-design drive system with gear reduction

petermccloud, 2019-08-09:
Drive system needs to be re-designed to reduce the propeller speed and change the layout to a standard quad rotor layout. Plan is to use belt drives to change the rotor speed and switch to separate belts for each rotor. This will also make the system more consistent with Titan.

petermccloud, 2019-08-09:
New pulleys will be GT2 profile. Belts will be either Gates GT3 belts or Jason Platinum Belts.
[Gates GT3 Design Guide](http://www.bearingsandindustrialsupply.com/pdf/power-grip-drive-design.pdf)
[Jason Platinum Design Guide](http://www.jasonindustrial.com/pdf/PLATINUM%20DESIGN%20MANUAL-2012-WEBSITE.pdf)

petermccloud, 2019-08-13:
Main belt specs:
Belt is 544 mm, 68 tooth Platinum belt, 35 mm wide. Engine pulley is 27 tooth, Main shaft pulley is 40 tooth.

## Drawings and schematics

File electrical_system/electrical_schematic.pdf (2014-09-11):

M

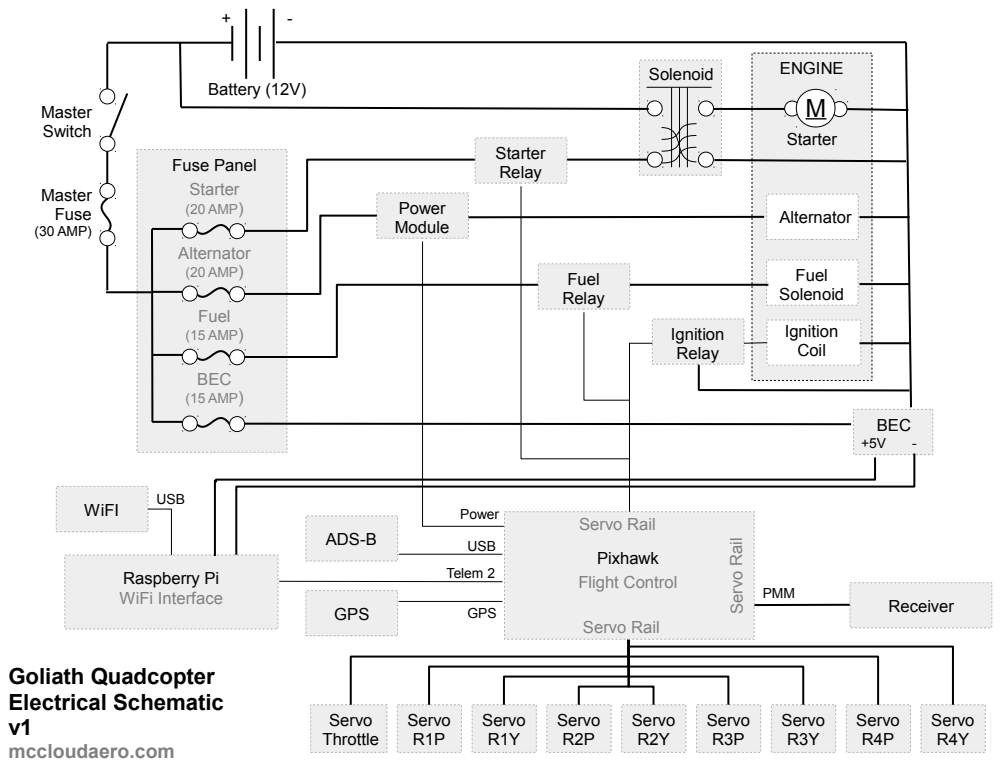
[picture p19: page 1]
Solenoid; Battery (12V); Master Switch; Master Fuse (30 AMP); Starter (20 AMP); Alternator (20 AMP); Fuel (15 AMP); Fuse Panel; BEC; Receiver; PMM; Servo R1P; Servo R1Y; Servo R2P; Servo R2Y; Servo R3P; Servo R3Y; Servo R4P; Servo R4Y; Servo Throttle; Servo Rail; Pixhawk; GPS; Starter; BEC (15 AMP); Alternator; Fuel Solenoid; Power Module; Starter Relay; Fuel Relay; Ignition Coil; Ignition Relay; ENGINE; Raspberry Pi; Telem 2; Power; Flight Control; WiFi Interface; WiFI; ADS-B; erv; ail; USB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

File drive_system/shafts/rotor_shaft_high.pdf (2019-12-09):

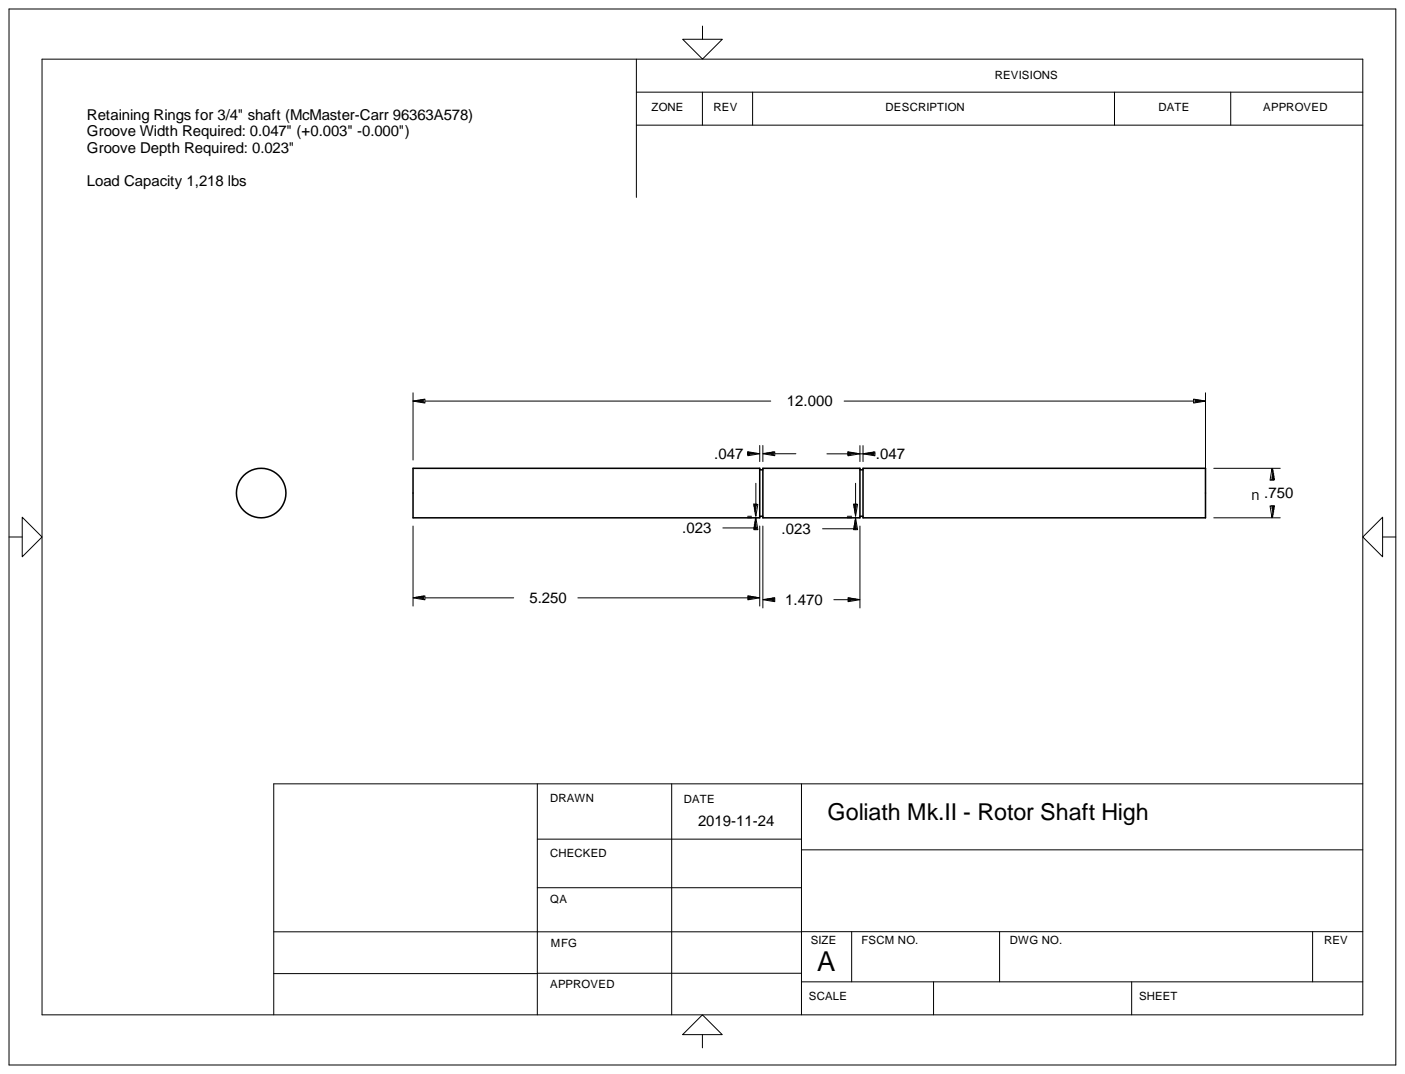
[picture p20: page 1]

REVISIONS

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

ZONE | REV | DESCRIPTION | DATE | APPROVED

Load Capacity 1,218 lbs

DRAWN | DATE 2019-11-24 | Goliath Mk.II - Rotor Shaft High

CHECKED

MFG | | SIZE A | FSCM NO. | DWG NO. | REV

APPROVED

SCALE | SHEET

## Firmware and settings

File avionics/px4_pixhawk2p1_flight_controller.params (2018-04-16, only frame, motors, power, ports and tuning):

1	1	BAT_A_PER_V	15.391030311584472656	9
1	1	BAT_CAPACITY	-1.000000000000000000	9
1	1	BAT_CNT_V_CURR	0.000805664050858468	9
1	1	BAT_CNT_V_VOLT	0.000805664050858468	9
1	1	BAT_CRIT_THR	0.070000000298023224	9
1	1	BAT_EMERGEN_THR	0.050000000745058060	9
1	1	BAT_LOW_THR	0.150000005960464478	9
1	1	BAT_N_CELLS	6	6
1	1	BAT_R_INTERNAL	-1.000000000000000000	9
1	1	BAT_SOURCE	0	6
1	1	BAT_V_CHARGED	2.200000047683715820	9
1	1	BAT_V_DIV	12.187596321105957031	9
1	1	BAT_V_EMPTY	1.750000000000000000	9
1	1	BAT_V_LOAD_DROP	0.500000000000000000	9
1	1	BAT_V_OFFS_CURR	0.000000000000000000	9
1	1	BAT_V_SCALE_IO	10000	6
1	1	MC_PITCHRATE_D	0.003000000026077032	9
1	1	MC_PITCHRATE_FF	0.000000000000000000	9
1	1	MC_PITCHRATE_I	0.050000000745058060	9
1	1	MC_PITCHRATE_MAX	220.000000000000000000	9
1	1	MC_PITCHRATE_P	0.150000005960464478	9
1	1	MC_PITCH_P	6.500000000000000000	9
1	1	MC_PITCH_TC	0.200000002980232239	9
1	1	MC_ROLLRATE_D	0.003000000026077032	9
1	1	MC_ROLLRATE_FF	0.000000000000000000	9
1	1	MC_ROLLRATE_I	0.050000000745058060	9
1	1	MC_ROLLRATE_MAX	220.000000000000000000	9
1	1	MC_ROLLRATE_P	0.150000005960464478	9
1	1	MC_ROLL_P	6.500000000000000000	9
1	1	MC_ROLL_TC	0.200000002980232239	9
1	1	MC_YAWRATE_D	0.000000000000000000	9
1	1	MC_YAWRATE_FF	0.000000000000000000	9
1	1	MC_YAWRATE_I	0.100000001490116119	9
1	1	MC_YAWRATE_MAX	200.000000000000000000	9
1	1	MC_YAWRATE_P	0.200000002980232239	9
1	1	MC_YAWRAUTO_MAX	45.000000000000000000	9
1	1	MC_YAW_FF	0.500000000000000000	9
1	1	MC_YAW_P	2.799999952316284180	9
1	1	MOT_SLEW_MAX	0.000000000000000000	9
1	1	PWM_MAIN_REV1	0	6
1	1	PWM_MAIN_REV2	0	6
1	1	PWM_MAIN_REV3	0	6
1	1	PWM_MAIN_REV4	0	6
1	1	PWM_MAIN_REV5	0	6
1	1	PWM_MAIN_REV6	0	6
1	1	PWM_MAIN_REV7	0	6
1	1	PWM_MAIN_REV8	0	6
1	1	PWM_MAIN_TRIM1	0.000000000000000000	9
1	1	PWM_MAIN_TRIM2	0.000000000000000000	9
1	1	PWM_MAIN_TRIM3	0.000000000000000000	9
1	1	PWM_MAIN_TRIM4	0.000000000000000000	9
1	1	PWM_MAIN_TRIM5	0.000000000000000000	9
1	1	PWM_MAIN_TRIM6	0.000000000000000000	9
1	1	PWM_MAIN_TRIM7	0.000000000000000000	9
1	1	PWM_MAIN_TRIM8	0.000000000000000000	9
1	1	SYS_AUTOSTART	4002	6

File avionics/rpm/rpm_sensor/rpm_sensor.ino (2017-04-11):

/*
Arduino RPM Sensor based on Trinket Pro 5V
by
Peter McCloud - McCloud Aero Corp (http://mccloudaero.com)

Inspired by:
Hall Effect Sensor Project on DIY Hacking (http://diyhacking.com)
by Arvind Sanjeev
*/

 const bool debug_mode = false;

 volatile byte revolutions;
 unsigned int rpm;
 unsigned long timeold;
 
 void setup()
 {
   Serial.begin(115200);
   // Trinket Pro: Pins 2 & 3 are available for interupts, Pin 2 is used by USB
   // 0 - Pin 2
   // 1 = Pin 3
   attachInterrupt(1, magnet_detect, RISING);//Initialize the intterrupt pin (Arduino digital pin 2)
   revolutions = 0;
   rpm = 0;
   timeold = 0;
 }
 void loop()//Measure RPM
 {
   if (revolutions >= 20) { 
     rpm = 60*1000/(millis() - timeold)*revolutions;
     timeold = millis();
     revolutions = 0;
     //Serial.println(rpm,DEC);
   }
 }
 void magnet_detect()//This function is called whenever a magnet/interrupt is detected by the arduino
 {
   revolutions++;
   if (debug_mode == true) {
     Serial.println("detect");
     // Blink the LED on Interupt
     digitalWrite(LED_BUILTIN, HIGH);   // turn the LED on (HIGH is the voltage level)
     delay(1000);                       // wait for a second
     digitalWrite(LED_BUILTIN, LOW);    // turn the LED off by making the voltage LOW
   }
 }

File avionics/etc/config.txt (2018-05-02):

# Goliath Quadcopter
set VEHICLE_TYPE mc
set MAV_TYPE 0

# Main
set MIXER goliath_mkii
set PWM_OUT 1234

# Aux
set MIXER_AUX goliath_mkii
set PWM_AUX_OUT 1234

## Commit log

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2014-07-12 Added rotors/rotor_ccw_top_drill_holes.nc which is used to drill the mounting and alignment holes. Modified rotors/rotor_ccw_top_finish_x_only.nc to include machining the top surface to account for r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
2014-07-20 Modified bottom rough tool path to use a quarter inch tool. Modified bottom finish x path to include machining the top of the surface. Added all files for the Clockwise (CW) rotor.
2014-08-15 Adding machining files for cutting crush plates
    [crush_plate.stl]
2014-08-16 Updated Crush Plate tool paths to add additional retract height Adding redrill tool path for cleaning up the drill holes after fiberglassing
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2014-09-27 Updated Belt and Pulley Layout. Fixed rotation error and added belt directions.
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2014-10-14 Updating Cutting Guides for latest changes in frame. Also added cutting guides for the all-thread
2014-10-15 Updating cutting guides to add thread pitch. Added initial copy of parts list.
    [parts_list.ods]
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2014-12-06 Added chain vs belt drive information
    [roller_chain_vs_belt_drive.ods]
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2015-01-25 Changed orientation of Frame. Was oriented to Deck, flipped over to orient for the entire vehicle. Updated Contraints.
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2015-01-31 Added Vertical_Support_B to the Frame Added Upper Set of Center Beams Fixed alignment of Cross Beams with Side Beams (Off by 1 Hole)
2015-02-02 Removed End Beams, Bolts and Re did constraints. This is to correct for the fact that End Beams are added later.
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2015-02-14 Added disc loading spreadsheet. Used to calculator required horsepower
    [disc_loading.ods]
2015-03-07 Updated Disc Loading Calculator and added screenshots
    [disc_loading.ods]
2015-11-14 fixed typos in parts list
    [parts_list.ods]
2015-11-14 fixed typos in disc loading
    [disc_loading.ods]
2015-11-14 removed rotors directory. Rotors have their own repository now
    [crush_plate.stl]
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2015-11-14 initial engine choices spreadsheet
    [engine_choices.ods]
2015-11-14 initial rotor pulley design
    [91257A557.STEP, rotor_pulley_design.ods]
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2015-11-28 updated parts list to reflect new rtor pulleys
    [parts_list.ods]
2015-12-02 updated parts list to include the rotor pulley breakdown
    [parts_list.ods]
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2016-01-09 added ehang 184 analysis comparisons
    [ehang_184_disc_loading.ods]
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2016-01-25 added rotor pulley bearings
    [2780T420.STEP]
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2016-01-25 update parts list to reflect updated bearings
    [parts_list.ods]
2016-02-02 added coordinates for drive belts
    [belt_layout.ods]
2016-02-03 added belts to coordinates plot
    [belt_layout.ods]
2016-02-04 added belt tension calculatio method 1
    [belt_layout.ods]
2016-02-05 added pulley names to belt span lists
    [belt_layout.ods]
2016-02-05 added tension method 2
    [belt_layout.ods]
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2016-02-21 updated rotor bearings for larger rotor shafts
    [2780T420.STEP, 2780T43.STEP, parts_list.ods]
2016-02-21 updated rotor shafts from 5/8 to 3/4
    [5947K150.STEP]
2016-02-21 replaced E-clips for retaining rings for rotor pulleys
    [96363A578.STEP]
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2016-03-13 initial commit for goliath specific pixhawk files
    [config.txt]
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2016-04-20 added engine datasheets and crudeCAD object
    [engine.stp]
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2016-04-26 added frame3dd setup info, template file
    [tube_properties.ods]
2016-05-03 minor updates to pulley layout spreadsheet
    [belt_layout.ods]
2016-05-03 moved engine choices spreadsheet to engine dir
    [engine_choices.ods]
2016-05-03 added intial spreadsheet with structure loads
    [structure_loads.ods]
2016-05-04 fixed error in tension method 2 calculations
    [belt_layout.ods]
2016-05-04 completed initial structure loads compilation
    [structure_loads.ods]
2016-05-06 updated template to include actual tube properties
    [tube_properties.ods]
2016-05-09 structure analysis template rough draft completed
    [structure_loads.ods, tube_properties.ods]
2016-05-14 reworked cross members
    [tube_properties.ods]
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2016-05-15 added frame weight estimate
    [tube_properties.ods]
2016-05-16 updated rivet grip lengths and quantities
    [tube_properties.ods]
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2016-05-22 added frame_nodes for CAD and initial CAD object
    [frame_nodes.csv]
2016-05-27 updated engine choices
    [engine_choices.ods]
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2016-06-04 made shaft_mount dir
    [rotor_shaft_mount_A.stl]
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2016-06-04 added upper frame arms
    [frame_nodes.csv]
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2016-07-09 updates to rotor shaft mount and tool paths
    [rotor_shaft_mount_A.stl]
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2016-07-27 added rotor_shaft_mount_C
    [rotor_shaft_mount_C.stl]
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2016-08-01 changed location of idler #3 in the spreadsheet
    [belt_layout.ods]
2016-10-02 added spreadsheet for rudder sizing
    [rudder_sizing.ods]
2016-10-10 initial work on 3rd gen rotors
    [disc_loading.ods]
2016-11-04 updates to power analysis
    [disc_loading.ods]
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2016-12-02 test log and data updates up to MkII test 10
    [test_log.ods]
2016-12-03 added idler shaft mount
    [idler_shaft_mount_no_holes.stl]
2016-12-05 updated idler shaft hole size tolerance
    [idler_shaft_mount_no_holes.stl]
2016-12-12 added pitch rate comparisons
    [pitch_rate_comparison.ods]
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2017-02-06 test log updates through mkII test 15
    [test_log.ods]
2017-02-27 updated disc loading with gamma candidates
    [disc_loading.ods]
2017-03-18 added intial files for arduino rpm sensor
    [rpm_sensor.fzz]
2017-04-06 updates to rpm sensor fritzing
    [rpm_sensor.fzz]
2017-04-07 updated rpm sensor drawings
    [rpm_sensor.fzz]
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2018-04-16 added information on computing battery parameters for 12V AGM battery
    [battery_parameters_calc.ods]
2018-04-16 added parameters file for pixhawk2 controller
    [px4_pixhawk2p1_flight_controller.params]
2018-04-25 changes to goliath avionics configuration to remove yaw from the mixer for testing
    [config.txt]
2018-05-02 fixed aux mixer issues with latest avionics changes
    [config.txt]
2018-11-02 added dimensions of vehicle mount
    [config.txt]
2018-11-03 updates to avionics setup
    [config.txt]
2019-03-31 added grid fin sizing calcs OBSOLETE
    [grid_fin_sizing.ods]
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
